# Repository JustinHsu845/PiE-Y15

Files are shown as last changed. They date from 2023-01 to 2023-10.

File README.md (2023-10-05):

# Power Distribution Board
## Pioneers in Engineering Year 2022-2023
---
We are basing our design on the Y9 PDB design. We will use a toggle switch instead of the circuit breaker to power on the device, and a fuse in series with the battery as a safety feature. This is an effort to cut costs.  
  
**Features:**  
- Anderson Connectors (A{1-5}) provide 12v power to motor controllers and other components that require 12v.
- USB-A Ports (USB{1-3}) provide 5v power to Le Potato computer and other components that require 5v.
- USB-A Port (DATA1) sends serial data from the PDB to the Le Potato computer.
- Rocker Switch (Sw1) turns on the board, thereby turning on the robot.
- SPST Switch (Sw2) selects which network the robot should be connected to.
- Disable Buzzing Pins (J1) disables buzzing from low battery when shorted.

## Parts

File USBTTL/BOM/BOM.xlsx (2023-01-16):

Comment | Designator | Footprint
12MHz | Y1 | Crystal_HC49-U_Vertical
USB_Type_A_903-331A1011D10100 | USB1 | USB-A_female
CH340G | U1 | SOIC-16_3.9x9.9mm_P1.27mm
Conn_01x04 | J1 | PinHeader_1x04_P2.54mm_Vertical
22pF | C4,C3 | C_0603_1608Metric
0.1uF | C2,C1 | C_0603_1608Metric

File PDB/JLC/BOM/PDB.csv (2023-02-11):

Comment | Designator | Footprint
200 | R11,R7,R12,R10,R14,R9,R13,R8 | R_0603_1608Metric
10u | C2,C1 | CP_Radial_D5.0mm_P2.00mm
Conn_01x02 | J1 | PinHeader_1x02_P2.54mm_Vertical
USB | USB2,USB3,USB1,DATA1 | USB-A_female
10000 | R6,R2,R4 | R_0603_1608Metric
JST-XH_4-pin | Jst1 | JST_XH_B4B-XH-A_1x04_P2.50mm_Vertical
4_digit_7_segment_display | D3 | LED-SEG-TH_12P-L30.0-W13.7-P2.54-S10.16-BL
0.1uF | C3,C4 | C_0603_1608Metric
Buzzer | B1 | Buzzer
12MHz | Y1 | JYJE S1C12000VWFAC
22pF | C5,C6 | C_0603_1608Metric
Anderson_Horizontal | A2,A4,A5,A3,A1 | anderson_horizontal
30000 | R5,R3,R1 | R_0603_1608Metric
ProMicro | Pro1 | ProMicro-EnforcedTop
Fuseholder | F1 | Fuse Holder SMD
PCF8574 | U3 | PCF8574T
4700 | R20,R19 | R_0603_1608Metric
22 | R17,R18 | R_0603_1608Metric
Hole_R1.62mm | REF**,REF**,REF**,REF** | Hole_R1.62mm
s8050_JSMSEMI | Q1 | s8050 JSMSEMI
0.1u | C7 | C_0603_1608Metric
SW_SPDT | SW2 | DEALON SS-12D01-G3
BUCK_CONVERTER_5V | Converter1 | 5v_converter
3300 | R15 | R_0603_1608Metric
D-SWITCH_MR5-111-C5N-BB | Sw1 | Rocker Switch
CH340G | U2 | CH340g
1000 | R16 | R_0603_1608Metric
XT60_F | Batt1 | AMASS_XT60-M_1x02_P7.20mm_Vertical
Conn_01x04 | J2 | PinHeader_1x04_P2.54mm_Vertical

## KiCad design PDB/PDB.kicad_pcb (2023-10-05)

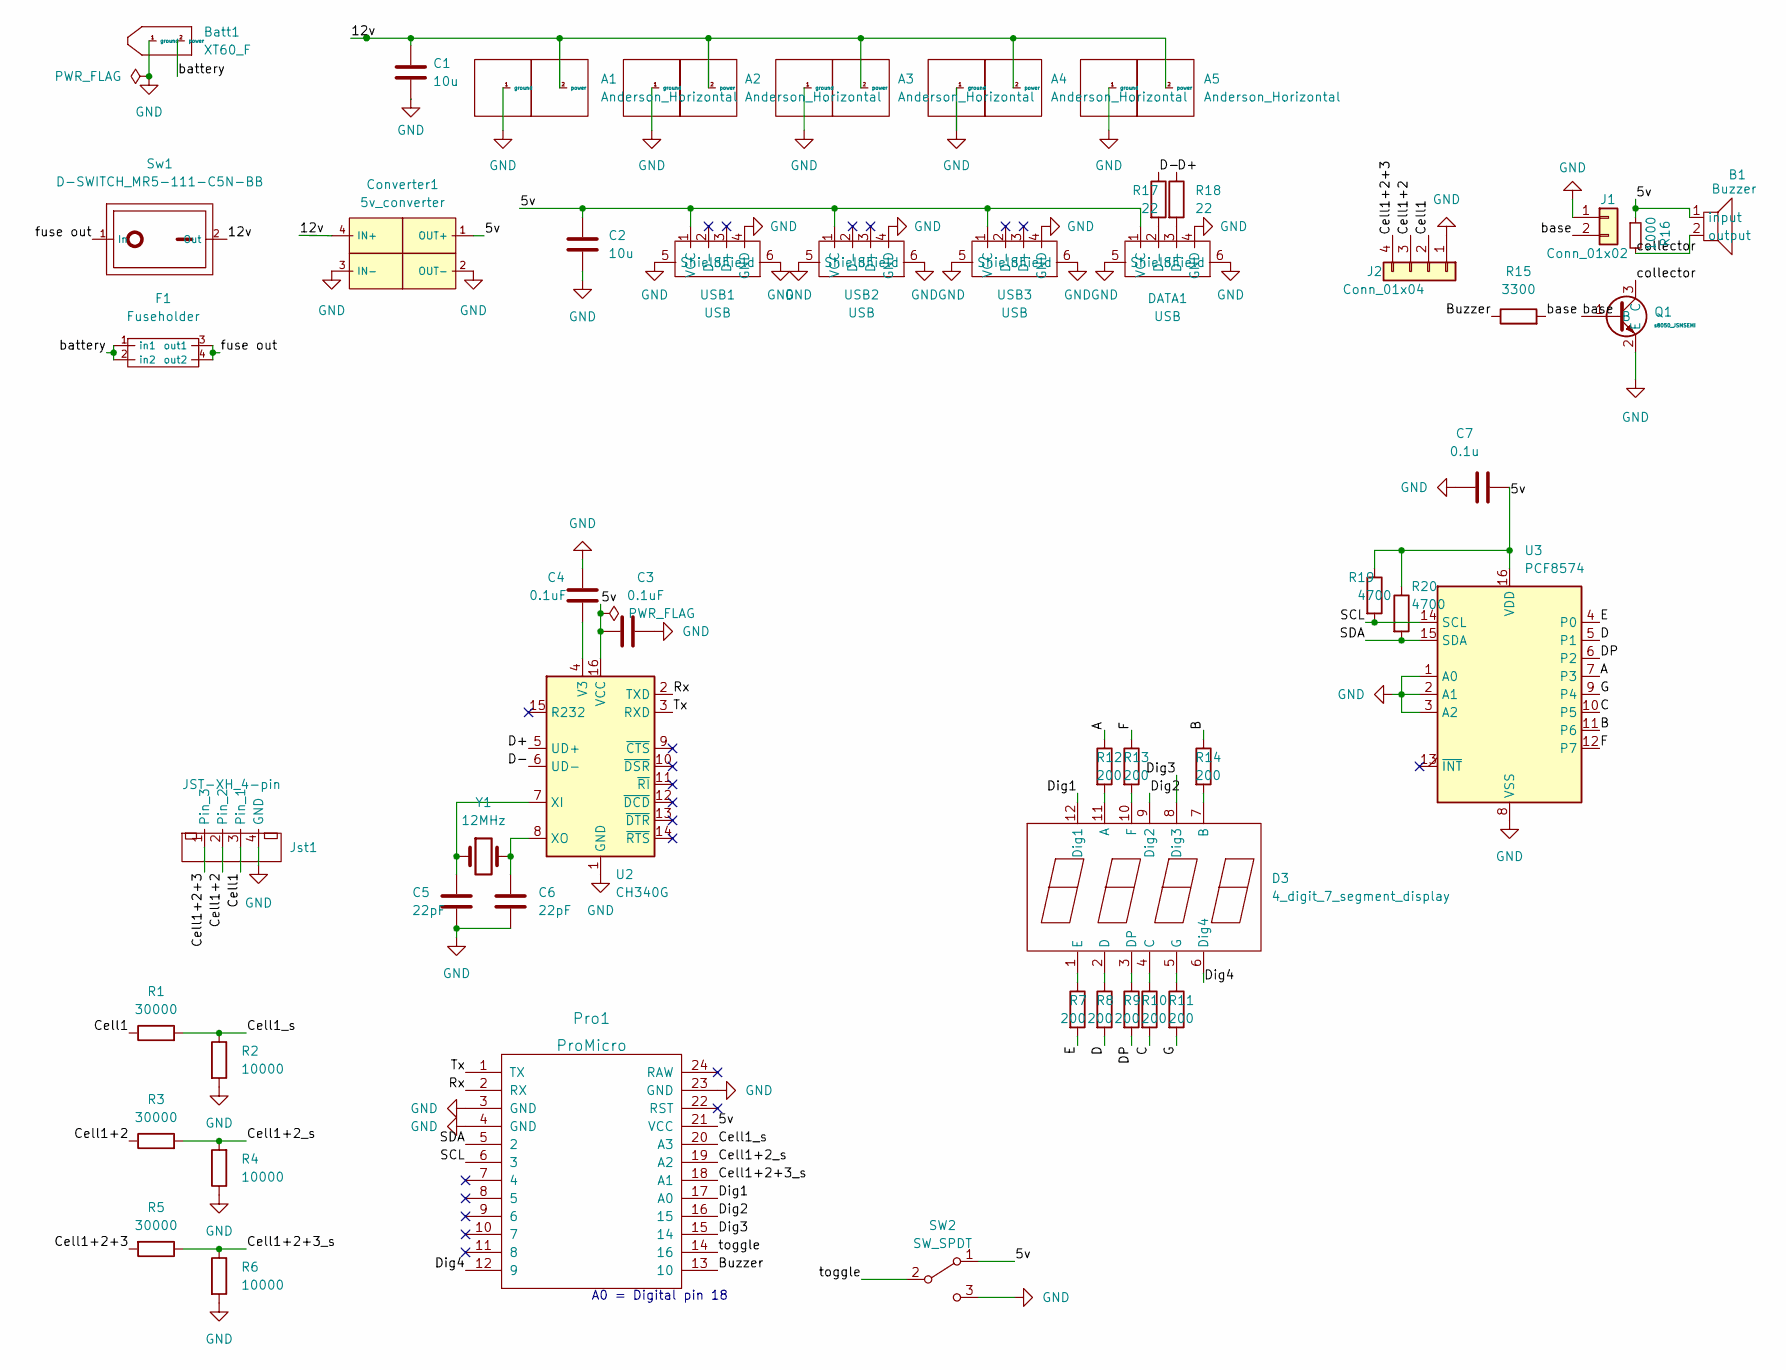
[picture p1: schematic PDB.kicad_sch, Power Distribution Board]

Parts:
A1, A2, A3, A4, A5: Anderson_Horizontal; anderson_horizontal
B1: Buzzer
Batt1: XT60_F; AMASS_XT60-M_1x02_P7.20mm_Vertical
C1, C2: 10u; CP_Radial_D5.0mm_P2.00mm
C3, C4: 0.1uF; C_0603_1608Metric
C5, C6: 22pF; C_0603_1608Metric
C7: 0.1u; C_0603_1608Metric
Converter1: 5v_converter
D3: 4_digit_7_segment_display; LED-SEG-TH_12P-L30.0-W13.7-P2.54-S10.16-BL
DATA1: USB; USB-A_female
F1: Fuseholder; Fuse Holder SMD
J1: Conn_01x02; PinHeader_1x02_P2.54mm_Vertical
J2: Conn_01x04; PinHeader_1x04_P2.54mm_Vertical
Jst1: JST-XH_4-pin; JST_XH_B4B-XH-A_1x04_P2.50mm_Vertical
Pro1: ProMicro; ProMicro-EnforcedTop
Q1: s8050_JSMSEMI; s8050 JSMSEMI
R1, R3, R5: 30000; R_0603_1608Metric
R2, R4, R6: 10000; R_0603_1608Metric
R7, R8, R9, R10, R11, R12, R13, R14: 200; R_0603_1608Metric
R15: 3300; R_0603_1608Metric
R16: 1000; R_0603_1608Metric
R17, R18: 22; R_0603_1608Metric
R19, R20: 4700; R_0603_1608Metric
SW2: SW_SPDT; DEALON SS-12D01-G3
Sw1: D-SWITCH_MR5-111-C5N-BB; Rocker Switch
U2: CH340G; CH340g
U3: PCF8574; PCF8574T
USB1, USB2, USB3: USB; USB-A_female
Y1: 12MHz; JYJE S1C12000VWFAC

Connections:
/5v: B1.1 (input), C2.1, C3.1, C7.2, Converter1.1 (OUT+), DATA1.1 (VCC), Pro1.21 (VCC), R16.1, R19.1, R20.1, SW2.1 (A), U2.16 (VCC), U3.16 (VDD), USB1.1 (VCC), USB2.1 (VCC), USB3.1 (VCC)
/12v: A1.2 (power), A2.2 (power), A3.2 (power), A4.2 (power), A5.2 (power), C1.1, Converter1.4 (IN+), Sw1.2 (Out)
/A: R12.1, U3.7 (P3)
/B: R14.1, U3.11 (P6)
/Buzzer: Pro1.13 (10), R15.1
/C: R10.2, U3.10 (P5)
/Cell1: J2.2, Jst1.3 (Pin_1), R1.1
/Cell1+2: J2.3, Jst1.2, R3.1
/Cell1+2+3: J2.4, Jst1.1 (Pin_3), R5.2
/Cell1+2+3_s: Pro1.18 (A1), R5.1, R6.1
/Cell1+2_s: Pro1.19 (A2), R3.2, R4.2
/Cell1_s: Pro1.20 (A3), R1.2, R2.1
/D: R8.2, U3.5 (P1)
/D+: R18.1, U2.5 (UD+)
/D-: R17.1, U2.6 (UD-)
/DP: R9.2, U3.6 (P2)
/Dig1: D3.12 (Dig1), Pro1.17 (A0)
/Dig2: D3.9 (Dig2), Pro1.16 (15)
/Dig3: D3.8 (Dig3), Pro1.15 (14)
/Dig4: D3.6 (Dig4), Pro1.12 (9)
/E: R7.2, U3.4 (P0)
/F: R13.1, U3.12 (P7)
/G: R11.2, U3.9 (P4)
/Rx: Pro1.2 (RX), U2.2 (TXD)
/SCL: Pro1.6 (3), R19.2, U3.14 (SCL)
/SDA: Pro1.5 (2), R20.2, U3.15 (SDA)
/Tx: Pro1.1 (TX), U2.3 (RXD)
/base: J1.2, Q1.1 (B), R15.2
/battery: Batt1.2 (power), F1.1 (in1), F1.2 (in2)
/collector: B1.2 (output), Q1.3 (C), R16.2
/fuse out: F1.3 (out1), F1.4 (out2), Sw1.1 (In)
/toggle: Pro1.14 (16), SW2.2 (B)
GND: A1.1 (ground), A2.1 (ground), A3.1 (ground), A4.1 (ground), A5.1 (ground), Batt1.1 (ground), C1.2, C2.2, C3.2, C4.2, C5.2, C6.2, C7.1, Converter1.2 (OUT-), Converter1.3 (IN-), DATA1.4 (GND), DATA1.5 (Shield), DATA1.6 (Shield), J1.1, J2.1, Jst1.4 (GND), Pro1.3 (GND), Pro1.4 (GND), Pro1.23 (GND), Q1.2 (E), R2.2, R4.1, R6.2, SW2.3 (C), U2.1 (GND), U3.1 (A0), U3.2 (A1), U3.3 (A2), U3.8 (VSS), USB1.4 (GND), USB1.5 (Shield), USB1.6 (Shield), USB2.4 (GND), USB2.5 (Shield), USB2.6 (Shield), USB3.4 (GND), USB3.5 (Shield), USB3.6 (Shield)
unnamed: C4.1, U2.4 (V3)
unnamed: C5.1, U2.7 (XI), Y1.1
unnamed: C6.1, U2.8 (XO), Y1.2
unnamed: D3.1 (E), R7.1
unnamed: D3.2 (D), R8.1
unnamed: D3.3 (DP), R9.1
unnamed: D3.4 (C), R10.1
unnamed: D3.5 (G), R11.1
unnamed: D3.7 (B), R14.2
unnamed: D3.10 (F), R13.2
unnamed: D3.11 (A), R12.2
unnamed: DATA1.2 (D-), R17.2
unnamed: DATA1.3 (D+), R18.2

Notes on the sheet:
A0 = Digital pin 18

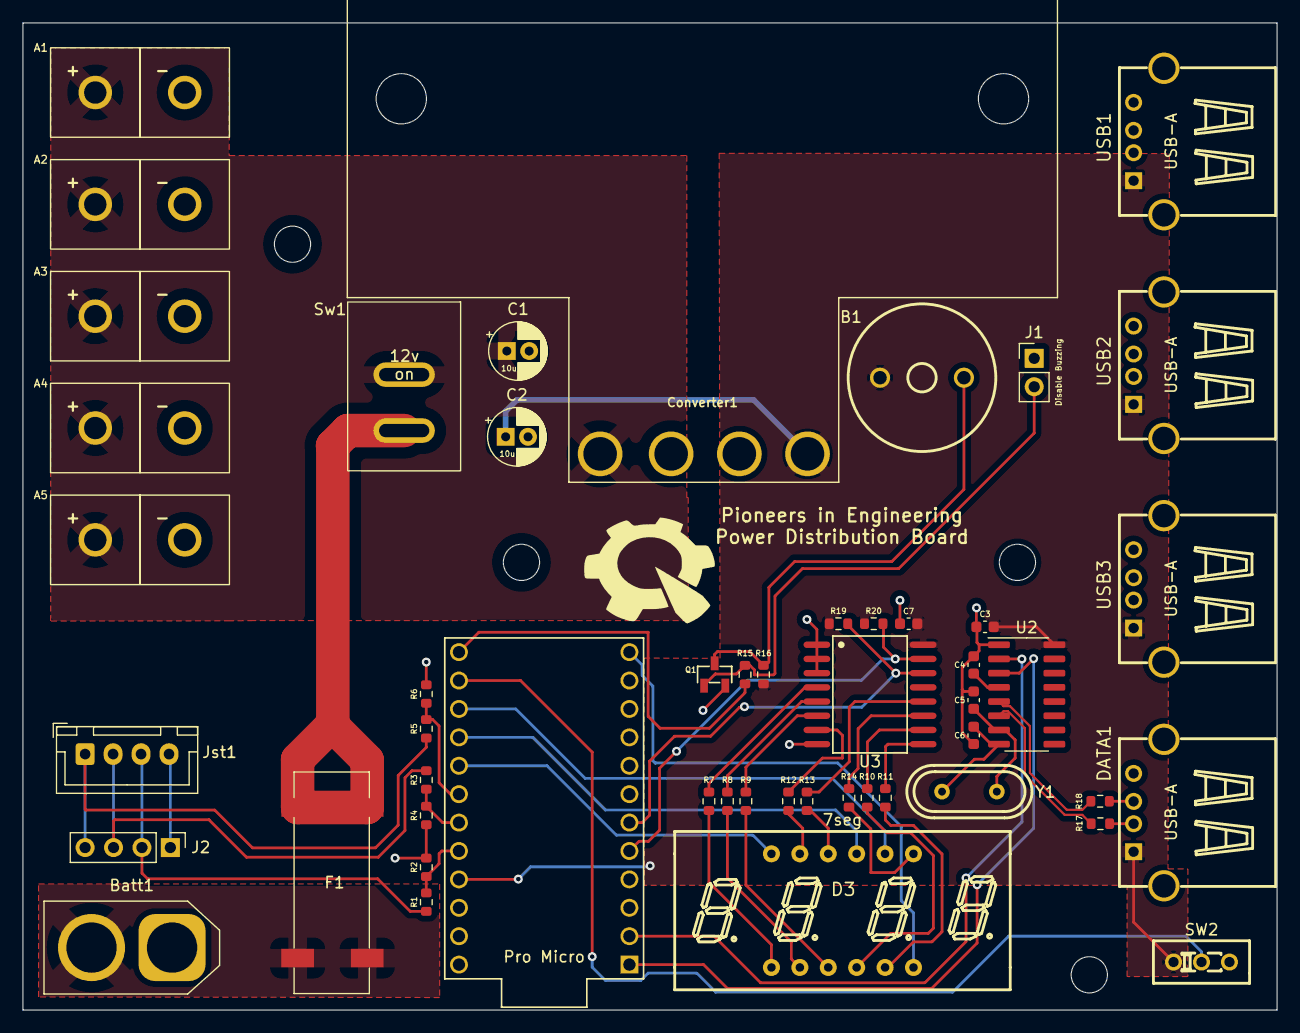
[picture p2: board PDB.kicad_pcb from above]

Board: 2 copper layers, 112.1 x 88.3 mm, 51 parts (0 on the bottom side), 46 nets.

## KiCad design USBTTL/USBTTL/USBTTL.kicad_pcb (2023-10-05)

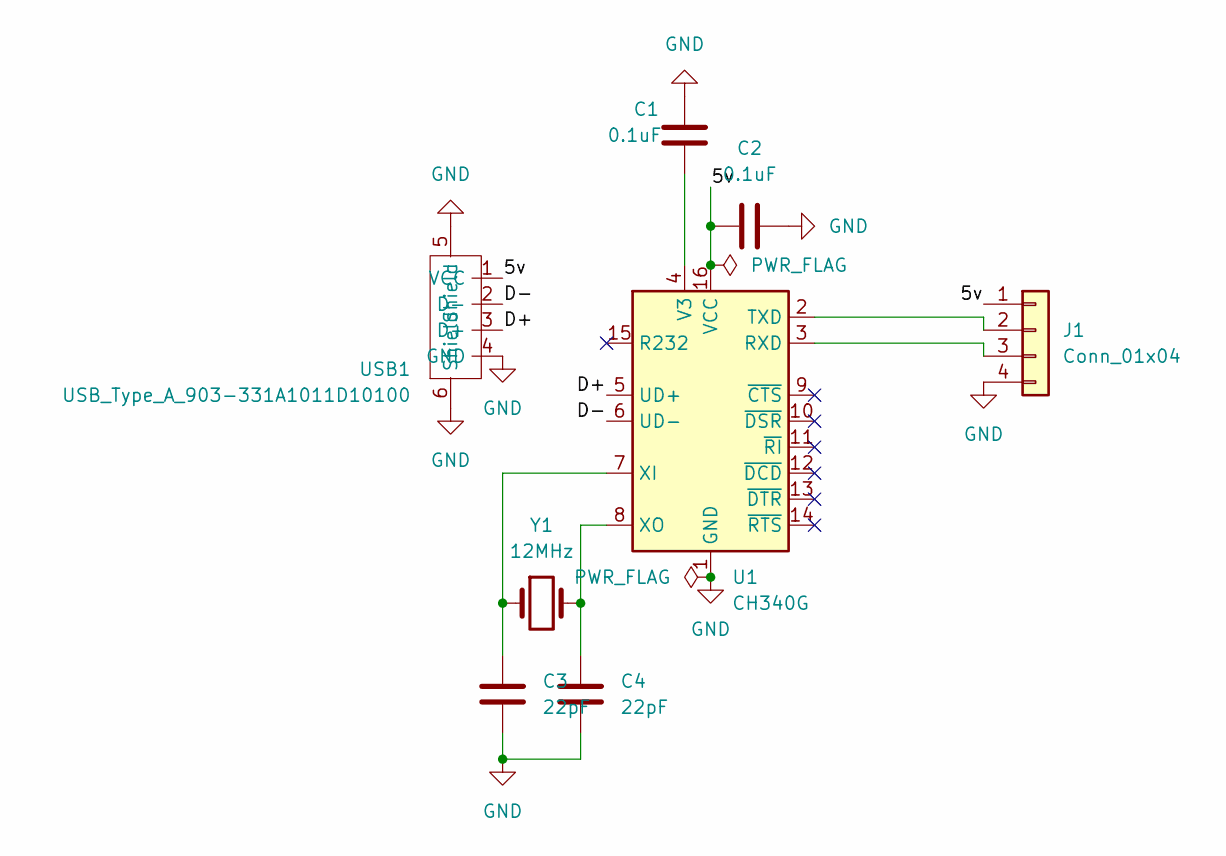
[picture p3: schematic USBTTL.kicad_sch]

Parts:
C1, C2: 0.1uF; C_0603_1608Metric
C3, C4: 22pF; C_0603_1608Metric
J1: Conn_01x04; PinHeader_1x04_P2.54mm_Vertical
U1: CH340G; SOIC-16_3.9x9.9mm_P1.27mm
USB1: USB_Type_A_903-331A1011D10100; USB-A_female
Y1: 12MHz; Crystal_HC49-U_Vertical

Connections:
/5v: C2.1, J1.1, U1.16 (VCC), USB1.1 (VCC)
/D+: U1.5 (UD+), USB1.3 (D+)
/D-: U1.6 (UD-), USB1.2 (D-)
GND: C1.2, C2.2, C3.2, C4.2, J1.4, U1.1 (GND), USB1.4 (GND), USB1.5 (Shield), USB1.6 (Shield)
unnamed: J1.2, U1.2 (TXD)
unnamed: J1.3, U1.3 (RXD)
unnamed: C1.1, U1.4 (V3)
unnamed: C3.1, U1.7 (XI), Y1.1
unnamed: C4.1, U1.8 (XO), Y1.2

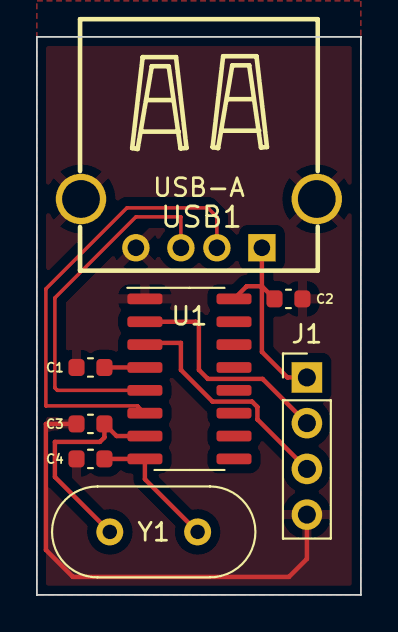
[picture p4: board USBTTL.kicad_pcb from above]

Board: 2 copper layers, 18.0 x 31.0 mm, 8 parts (0 on the bottom side), 9 nets.

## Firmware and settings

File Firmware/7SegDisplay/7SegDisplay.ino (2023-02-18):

#include <Wire.h>

#define expander B0100000 

#define D1 A0
#define D2 15
#define D3 14
#define D4 9
#define BUZZER 10
#define Cell1 A3
#define Cell2 A2
#define Cell3 A1
#define TOGGLE 16
#include "array.h"
#include "functions.h"

void setup() {     
  Serial.begin(9600);   
  Serial1.begin(9600);        

  pinMode(D1, OUTPUT);  
  pinMode(D2, OUTPUT);  
  pinMode(D3, OUTPUT);  
  pinMode(D4, OUTPUT); 

  pinMode(A3, INPUT);
  pinMode(A2, INPUT);
  pinMode(A1, INPUT);
  
  pinMode(BUZZER, OUTPUT);

  pinMode(TOGGLE, 16);

  pinMode(0, OUTPUT);
  pinMode(1, INPUT);
  
  Wire.begin();

}

char network_switch = -1;
//long previousTime = 0;
// the loop routine runs over and over again forever:
void loop() {
  //unsigned long currentTime = millis();
  analogReference(DEFAULT);
  //float* voltages = parseVoltage(analogRead(Cell1), analogRead(Cell2), analogRead(Cell3));
  float r_v1 = average(Cell1, 50);
  float v_v1 = r_v1 * 20.3/1023.0;
  String o_v1 = DisplayChars(String(v_v1));
  
  float r_v2 = average(Cell2, 50);
  float v_v2 = (r_v2 * 20.1/1023.0) - v_v1;
  String o_v2 = DisplayChars(String(v_v2));
  
  float r_v3 = average(Cell3, 50);
  float v_v3 = (r_v3 * 20.03/1023.0) - v_v2 - v_v1;
  String o_v3 = DisplayChars(String(v_v3));
  
  float r_all = average(Cell3, 50);
  float v_all = r_v3 * 20.03/1023.0;
  String o_all = DisplayChars(String(v_all));

  if (v_all < 11.5 || v_v1 < 3.8 || v_v2 < 3.8 || v_v3 < 3.8) {
  tone(10, 800);
  } else if (v_all > 12 && v_v1 > 4.0 && v_v2 > 4.0 && v_v3 > 4.0) {
    noTone(BUZZER);
  }
  
  Serial.println(digitalRead(TOGGLE));
  
  displayString("CEL1", 2000);
  displayString(o_v1, 2000);
  displayString("CEL2", 2000);
  displayString(o_v2, 2000);
  displayString("CEL3", 2000);
  displayString(o_v3, 2000);
  displayString("ALL ", 2000);
  displayString(o_all, 2000);

}

void displayString(String phrase, int length) {
  for (int i = 0; i < length/8; i++) {
    if (digitalRead(TOGGLE) != network_switch) {
      network_switch = digitalRead(TOGGLE);
      Serial1.println(digitalRead(TOGGLE));
    }
    printDigit(phrase[0], D1);
    delay(2);
    printDigit(phrase[1], D2);
    delay(2);
    printDigit(phrase[2], D3);
    delay(2);
    printDigit(phrase[3], D4);
    delay(2);
  }
}


/* gets the average values from an analog pin.
   Returns the averaged value of the pin. */
float average(int pin, int samples) {
  float sum = 0.0;
  for (int i = 0; i < samples; i++) {
    sum += analogRead(pin);
  }
  float average = sum / samples;
  return average;
}

void expanderWrite(byte _data) {
  Wire.beginTransmission(expander);
  Wire.write(_data);
  Wire.endTransmission(); 
}

void reset() { 
  digitalWrite(D1, LOW);
  digitalWrite(D2, LOW);
  digitalWrite(D3, LOW);
  digitalWrite(D4, LOW);
  expanderWrite(0b11111111);
  //for(byte i = 0 ; i < 8 ; i++){
    //digitalWrite(seg[i], HIGH); //mode = 1; for each segment, 1 = off and 0 = on
  //}
}

int printDigit(char Chara, int digitPort) { 
  reset(); 
  int character = -1;
  digitalWrite(digitPort, HIGH);
  for(int i = 0 ; i < charsInArray ; i++) {
    if (Chara == Char[i][1]) { //set character equal to the corresponding array index
     character = i;
    }
  }
  expanderWrite(~Char[character][0]);
  
}

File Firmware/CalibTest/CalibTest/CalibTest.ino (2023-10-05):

void setup() {
  // put your setup code here, to run once:
  pinMode(A1, INPUT);
  Serial.begin(9600);
}

int counter = 0;
float ref = 5.000;
void loop() {
  // put your main code here, to run repeatedly:
  int value = analogRead(A1);
  float voltage = value * (ref/1023);
  Serial.print("Reading: ");
  Serial.print(voltage);
  Serial.println("v");
  Serial.print("Ref: ");
  Serial.print(ref);
  Serial.println("v");
  if (voltage > 2.5) { //We will input 2.5v, should read 511 or 512
    ref -= 0.005;
    Serial.print("Calibration (overshoot) attempt: ");
    Serial.println(counter);
  } else if (voltage < 2.5) {
    ref += 0.005;
    Serial.print("Calibration (undershoot) attmpt: ");
    Serial.println(counter);
  } else {
    Serial.println("Calibration Complete!");
  }
  counter += 1;
  delay(100);
}

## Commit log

2022-11-02 started schematic
    [PDB.kicad_pcb, PDB.kicad_sch]
2022-11-02 Drafted battery indicator, added libraries
    [PDB.kicad_sch]
2022-11-05 Added anderson connector horizontal
2022-11-06 Put andersons on PCB, decoup cap needs footprint
    [PDB.kicad_pcb, PDB.kicad_sch]
2022-11-06 Fixed polarity of anderson_horizontal footprint
2022-11-07 added footprint to de cap
    [PDB.kicad_pcb, PDB.kicad_sch]
2022-11-07 added 5v rail and molex connectors
    [PDB.kicad_pcb, PDB.kicad_sch]
2022-11-08 added Converter symbol/footprint
    [PDB.kicad_pcb, PDB.kicad_sch]
2022-11-15 updated schematic
    [PDB.kicad_sch]
2022-11-22 Updated PDB with USB, battery sense
2022-11-24 added arduino-cli
2022-11-29 Finished 7Seg display
    [PDB.kicad_sch]
2022-11-29 added usb, 7seg footprints
2022-11-30 fixed 5v pin on promicro symbol
2022-11-30 added resistors to common anode
    [PDB.kicad_sch]
2022-12-01 shortened printDisplay code
2022-12-16 don't remember what this update is?
    [PDB.kicad_sch]
2022-12-16 finished Schematic
    [PDB.kicad_sch]
2022-12-16 added rocker switch and fuse holder symbols
2022-12-16 updated with LED and precision resistor notes
2023-01-08 gonna actually do some work
    [PDB.kicad_sch]
2023-01-10 changed pin #
2023-01-10 Fixed seg dis and added buzzer amp circuit
    [PDB.kicad_sch]
2023-01-10 Fixed 7-seg and buzzer symbols to match 50 mil pin standard
2023-01-11 added Buzzer, Fuseholder, Rocker Switch
2023-01-11 Started footprints
    [PDB.kicad_pcb, PDB.kicad_sch]
2023-01-12 Put most components on board
    [PDB.kicad_pcb, PDB.kicad_sch]
2023-01-12 added footprint for s8050 smd
2023-01-13 Completed board layout
    [PDB.kicad_pcb, PDB.kicad_sch]
2023-01-13 I swear i didn't change anything
    [7SegDisplay.ino]
2023-01-13 fixed silkscreen clipped on usb-a female
2023-01-16 fixed pin numbers
2023-01-16 added FTDI chip
    [PDB.kicad_sch]
2023-01-16 USB-to-TTL adapter
    [BOM.xlsx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]
2023-01-18 revised layout for smaller size
    [PDB.kicad_pcb, PDB.kicad_sch]
2023-01-18 Added + and - on silkscreen
2023-01-18 Increased track size for USB
    [PDB.kicad_pcb]
2023-01-26 added a bunch of footprints
    [BOM.xlsx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]
2023-01-26 Finished board layout?
    [PDB-B_Cu.gbr, PDB-B_Mask.gbr, PDB-B_Paste.gbr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]
2023-02-08 ordered this ****
    [PDB-B_Cu.gbr, PDB-B_Mask.gbr, PDB-B_Paste.gbr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]
2023-02-11 fixed PDB layout
    [BOM.xlsx, PDB.kicad_pcb, PDB.kicad_sch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]
2023-02-11 created production files
    [PDB-B_Cu.gbr, PDB-B_Mask.gbr, PDB-B_Paste.gbr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]
2023-02-11 added team flag
    [PiE_team_flag fake.csv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]
2023-02-18 fixed all issues for this season
    [7SegDisplay.ino]
2023-06-19 Only PDB related stuff
    [PiE_team_flag fake.csv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]
2023-10-05 idk when this was
    [PDB.kicad_pcb, USBTTL.kicad_pcb]

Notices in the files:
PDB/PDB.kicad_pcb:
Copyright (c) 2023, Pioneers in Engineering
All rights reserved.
